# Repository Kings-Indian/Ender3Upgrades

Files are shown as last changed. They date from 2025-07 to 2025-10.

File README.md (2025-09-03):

# Raspberry Pi Magnetic PETG Case for Ender 3

A custom magnetic PETG case designed specifically for the Raspberry Pi Zero 2 W, featuring dual fan cooling, LED support, OPTIONAL screen mount (since people, including me, have computers for their 3D Printers), and camera integration. This case is designed to mount securely to an Ender 3 3D printer for enhanced cooling, monitoring, and lighting capabilities.

## Why I Made This Project

I needed a reliable cooling solution for my Raspberry Pi Zero 2 W that was running Klipper firmware for my Ender 3 printer. The standard cases available didn't provide adequate cooling for the continuous operation required during long print jobs. I also wanted to add LED lighting, a screen mount for better monitoring, and camera integration for timelapses. The magnetic attachment system makes it easy to remove and maintain without tools, while the modular design allows for easy upgrades and modifications.

## Features

- **Magnetic Attachment**: Tool-less assembly using neodymium magnets for easy maintenance
- **Dual 30mm Fans**: Perfect cooling for the Raspberry Pi Zero 2 W during long print jobs
- **LED Integration**: WS2812B strip support for ambient lighting and SK6812 RGBW strips for printer illumination
- **Modular Screen Mount**: Compatible with Waveshare 4.3" HDMI LCD for monitoring
- **Camera Mount**: Adjustable Raspberry Pi Camera Module 3 mount for 4K timelapses
- **Sound Dampening**: Integrated foam ball holders for vibration reduction
- **Cable Management**: Dedicated cable routing holes and access points
- **Klipper Integration**: Smart magnet cover printing using Klipper firmware

## Project Pictures
My current full assembly, in CAD:



### Screen Mount
Screen Mount Assembly (only really useful if u don thave a computer connected)

If you have a computer connected to your printer, this is HIGHLY RECOMMENDED: 



### Camera Integration
Camera Mount Assembly

### LED Lighting System


## Wiring Diagram

```
Raspberry Pi Zero 2 W
├── GPIO 18 → WS2812B LED Strip Data (printer lighting)
├── GPIO 21 → SK6812 RGBW <img width="1018" height="674" alt="463837668-74d05153-4630-4f8c-87a0-d8d51d3b4930" src="https://github.com/user-attachments/assets/d8a1b71c-9329-4780-9d65-e9ff1aa41fdf" />
Strip Data 
├── 5V → WS2812B LED Strip VCC
├── External 5V → SK6812 RGBW Strip VCC
├── GND → WS2812B LED Strip GND
├── External GND → SK6812 LED Strip GND
├── GND → SK6812 RGBW Strip GND
├── Micro HDMI → Waveshare 4.3" LCD
├── Camera Port → Raspberry Pi Camera Module 3
├── 5v →  Fan VCC
├──  GND → Fan GND
└── Micro USB → Power Supply
```
Wiring Diagram

)463837668-74d05153-4630-4f8c-87a0-d8d51d3b4930

## Bill of Materials (BOM
| Item No. | Product Name | Amazon Link | Quantity | Cost (USD) | Notes | Running Total (USD) |
|---|---|---|---|---|---|---|
| 1 | Transparent Polymaker PETG Filament | [Link](https://www.amazon.com/dp/B09DKMCNMW?tag=all3dptrx00131-20&th=1) | 1 | $22.99 | Clear PETG filament for 3D printing | $22.99 |
| 2 | WINSINN 30mm RGB Fan 5V (Pack of 4Pcs) | [Link](https://www.amazon.com/WINSINN-Hydraulic-Bearing-Brushless-30x10mm/dp/B087QDRKW9/) | 1 | $8.99 | RGB micro fans for electronics/3D printing | $31.98 |
| 3 | Waveshare 4.3inch Capacitive Touch Screen LCD | [Link](https://www.amazon.com/4-3inch-HDMI-LCD-Resolution-Capacitive/dp/B07MB9MYYS/) | 1 | $53.99 | Touch display compatible with Raspberry Pi | $85.97 |
| 4 | Neodymium Magnets 5mm x 3mm (60 Pack) | [Link](https://www.amazon.com/Magnets-Multi-use-Refrigerator-Neodymium-Whiteboard/dp/B0BJDZRHV7/) | 1 | $3.99 | Mini magnets for mounting and DIY | $89.96 |
| 5 | Raspberry Pi 02w | [Link](https://www.amazon.com/dp/B0DRRRZBMP?ref_=ppx_hzsearch_conn_dt_b_fed_asin_title_1) | 1 | $26.99 | Main single-board controller | $116.95 |
| 6 | SEZO WS2812B LED Strip Light 1M | [Link](https://www.amazon.com/SEZO-Individually-Addressable-Programmable-Non-Waterproof/dp/B097BX7LRT/) | 1 | $6.99 | Addressable RGB LED strip for effects | $123.94 |
| 7 | Ktehloy 400Pcs Threaded Inserts | [Link](https://www.amazon.com/mxuteuk-420PCS-Screws-Socket-Wrench/dp/B0CSWD34KJ/) | 1 | $13.49 | Brass heat-set inserts for plastic parts | $137.43 |
| 8 | mxuteuk M3 Screws Kit (420PCS) | [Link](https://www.amazon.com/TOP-VIGOR-Machine-Fastener-Motorcycle-Repairment/dp/B0D5CJXW8X/) | 1 | $9.99 | Assorted M3 screws for Pi and mounts | $147.42 |
| 9 | TOP-VIGOR M4-0.7 x 12mm Socket Screws (30PCS) | [Link](https://www.amazon.com/TOP-VIGOR-Machine-Fastener-Motorcycle-Repairment/dp/B0D5CJXW8X/) | 1 | $5.35 | Screws for camera mounting | $152.77 |
| 10 | Arducam Raspberry Pi Camera Module 3 | [Link](https://www.amazon.com/Arducam-Raspberry-Camera-Autofocus-15-22pin/dp/B0C9PYCV9S/) | 1 | $22.00 | 12MP autofocus camera for Pi | $174.77 |
| 11 | UeeKKoo DSI FPC Flexible Cable | [Link](https://www.amazon.com/UeeKKoo-Flexible-Raspberry-Display-Suitable/dp/B0D12TMQ6D/) | 1 | $4.99 | Ribbon cable for Raspberry Pi display | $179.76 |
| 12 | BTF-LIGHTING SK6812 RGBW LED Strip 1M | [Link](https://www.amazon.com/BTF-LIGHTING-Individually-Addressable-Flexible-Non-waterproof/dp/B079ZT9Q9X/) | 1 | $25.99 | RGBW LED strip with addressable control | $205.75 |
| 13 | Zugar Land Galaxy Foam Stress Balls (4 Pack) | [Link](https://www.amazon.com/Zugar-Land-Squeeze-Relaxable-Calming/dp/B0CZS91TNW/) | 1 | $6.99 | Stress relief or soft bumper component | $212.74 |

Total project development time: **23.5 hours**



**Youtube:**: [Link](https://youtube.com/shorts/PC3ZzvA6rok) 

**Reddit:**: [Link](https://www.reddit.com/r/Hack_Club/comments/1m0td3w/my_first_robot_beginner_tank_drive_based_robot/)

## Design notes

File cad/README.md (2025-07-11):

# CAD Source Files

This directory contains the CAD source files for the Raspberry Pi Magnetic PETG Case project.

## File Structure

### Main Directory
- `EnderUpgrades.zip` - Compressed archive containing all CAD files
- `README.md` - This documentation file

### EnderUpgrades Directory
The main project directory containing all component files organized by category:

#### PiControl+Case/
Core case components for the Raspberry Pi enclosure:
- `Case - PiCase.step` - Main Raspberry Pi 
- `Case - FanCase.step` - Fan housing
- `Case - ScreenMount.step` - Screen mounting 

#### LED/
Lighting system components:
- `LED Rail - Open.step` - LED strip mounting rail (left closed side)
- `LED Rail - Closed.step` - LED strip mounting rail (right open side)

#### Camera/
Camera mounting and positioning components:
- `CAM - Fixed.step` - Pi Case Mount 
- `CAM - Rotating Cam Holder.step` - Adjustable rotating camera holder
- `CAMCap.step` - Camera lens cover/protection component

#### Foam Ball Holder/
Vibration damping and support components:
- `foam ball holder - BallHolder.step` - Foam ball holder for vibration isolation

#### Assembly Files
- `Full Assembly.step` - Complete assembly showing all components together

## CAD Software

These files were created using Onshape at https://cad.onshape.com/documents/c014fa01068b7641a56239ac/w/543cb7cab706bdd0461ab360/e/c9c7937bcc8a5b3a582f31b2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 and exported in STEP format.

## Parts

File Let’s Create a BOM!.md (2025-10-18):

### As you create hardware projects for Blueprint, you will be required to include a BOM, or Bill of Materials, in .csv format. If you have any questions or suggestions, reach out in #blueprint-support or DM @Tanishq Goyal!

--- 
## What is a BOM? Why is this important?

A BOM, or Bill of Materials, is the comprehensive list of ==**all**== required parts that you need to manufacture a finished product. Writing a BOM involves creating a document with a clear, organized structure to list all components, parts, and raw materials needed to manufacture a product. Think of this as a recipe: you need to specify exactly how much of each ingredient is needed, along with accurate costs, to ensure the final product turns out correctly. This is one of the most important parts of an open-source hardware project, as it is impossible to build anything without materials. 

--- 
## What Is Included in Your BOM? 

In industrial BOMs, you will generally include information such as part numbers, part names, descriptions, manufacturer/manufacturing method, etc. If you are interested, check out [this BOM writing guide](https://durolabs.co/blog/bill-of-materials-example/)

![[Pasted image 20251017223635.png]]
>[!info] This is is what industry BOMs look like. Thankfully, you won't have to deal with that for Blueprint! This format is pretty widespread, with robotics teams listing parts similarly as well. 

However, for Blueprint, your BOMs will look vastly different and is much less complex.  Here are the bare minimums for what you need for your Blueprint BOM:

1. Product name
2. Product link
3. Product cost
4. Product amount

That's it! However, a good BOM exceeds the bare minimum requirement. A good BOM may include:

1. Product name
2. Product description
3. Product link
4. Product unit price
5. Product amount
6. Product running total.

I find that this format allows me to track my costs easily. Although the minimum BOM looks simpler, the second example is much easier to actually use and read as you work on your project. 

Here's an example! Note that these are flexible. I also included taxes in order to get the most accurate BOM possible. 

| Item | Description | Quantity | Unit Price ($) | Total Price ($) | URL | Running Total ($ with Tax) | |
| --- | --- | --- | --- | --- | --- | --- | --- |
| Lancer Long Hotend | Hotend | 1 | 34.99 | 34.99 | https://peopoly.net/products/magneto-x-lancer-melt-zone?variant=46839304225050 | 37.31 | |
| CPAP FAN | Part-cooling Fan | 1 | 19.99 | 19.99 | https://www.fabreeko.com/products/cpap-fan-10ws7040-hose-by-mellow | 58.62 | |
| 3010 FAN | Hotend Fan | 1 | 6.69 | 6.69 | https://www.aliexpress.us/item/3256808756746945.html | 65.78 | |
| BTT Microprobe | Bed-Leveling Probe | 1 | 18.99 | 18.99 | https://biqu.equipment/products/microprobe-v1-0-for-b1-printers-h2-extruders-ender-3 | 86.00 | |
| SKR Mini E3 V3.0 | MCU | 1 | 29.98 | 29.98 | https://biqu.equipment/products/bigtreetech-skr-mini-e3-v2-0-32-bit-control-board-for-ender-3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 | 117.97 | |
| MGN12H Linear Rail Carriage Block | Linear Rail | 1 | 22.93 | 22.93 | https://www.aliexpress.us/item/2251832643511407.html | 142.42 | |
| GT2 Timing Belt | Belt | 1 | 2.38 | 2.38 | https://www.aliexpress.us/item/3256805030553800.html | 144.96 | |

--- 

## How Do I Create a BOM?

Fortunately, there are tools that allow you to easily create a .csv file, without manually writing one. 

Here is an example using Google Sheets. I will use formulas to make the Total Price and Running Total automatically update. 

1. Total Price Formula. This is equivalent to the Unit Price times the quantity. 
![[Pasted image 20251017234942.png]]
You should then drag the blue circle on the bottom right corner to copy the formulas for the below cells. For more information on formatting with Google Sheets, check out this [basic Google Sheets formula guide!](https://www.youtube.com/watch?v=llkP9DxRAPI) 

2. Running Total. 
This calculation represents the cumulative total of purchases including sales tax. The formula is:

**Running Total = (Total Price × (1 + Sales Tax Rate)) + Previous Running Total**

##### Example: New Jersey Sales Tax (6.625%)

**Formula Structure:**
- **Tax Multiplier:** `1.06625` (1 + 0.06625)
- **Rounding:** Applied to nearest cent using `ROUND` function
- **First Item:** `=ROUND(Total Price × 1.06625, 2)`
  - **Example:** `=ROUND(D2*1.06625,2)`
  - ![[Pasted image 20251018003730.png]]
- **Subsequent Items:** `=ROUND(Total Price × 1.06625, 2) + Previous Running Total`
  - **Example:** `=ROUND(D3*1.06625,2)+G2`
  - ![[Pasted image 20251018003712.png]]

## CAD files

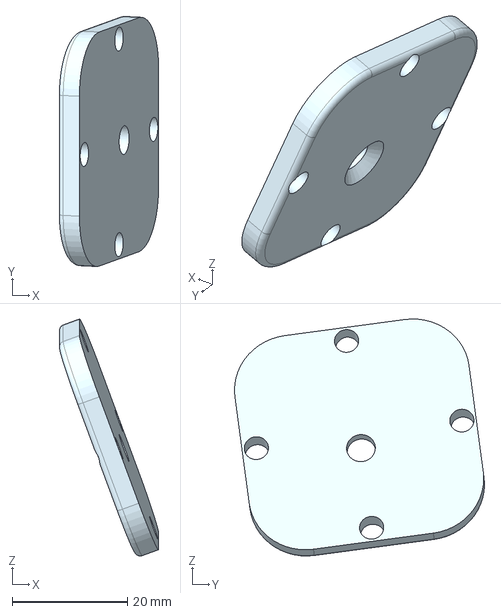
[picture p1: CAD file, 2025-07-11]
cad/EnderUpgrades/Camera/CAMCap.step
17.2 x 43.4 x 41.1 mm

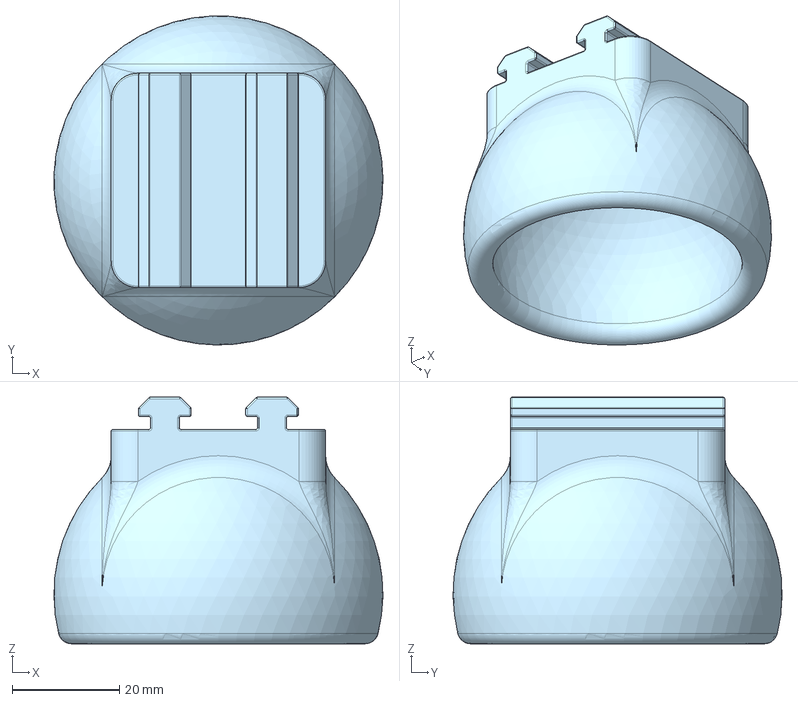
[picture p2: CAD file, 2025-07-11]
cad/EnderUpgrades/Foam Ball Holder/foam ball holder - BallHolder.step
61.4 x 61.4 x 46.0 mm

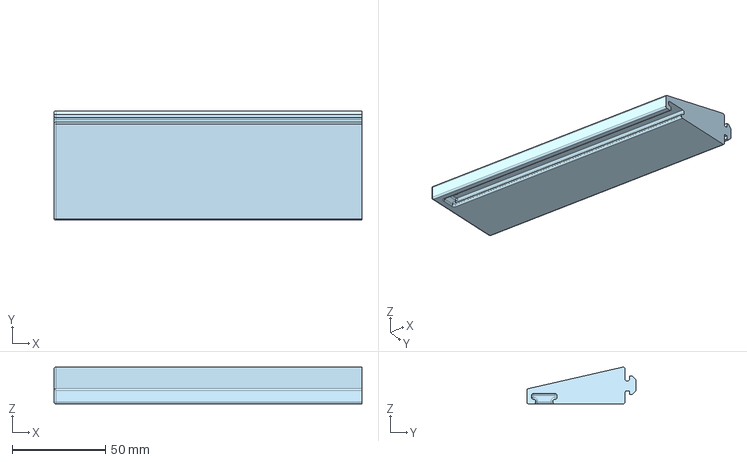
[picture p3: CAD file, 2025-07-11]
cad/EnderUpgrades/LED/LED Rail - Closed.step
165.0 x 58.7 x 19.7 mm

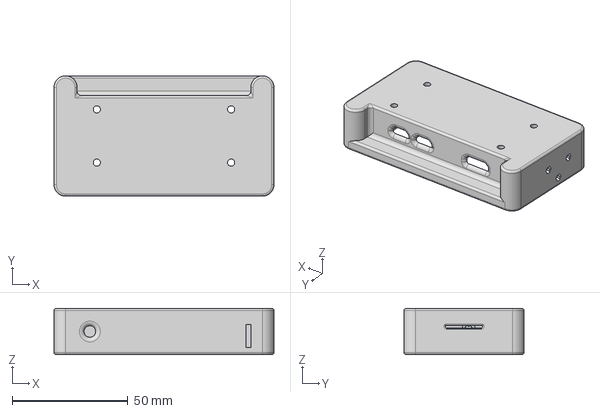
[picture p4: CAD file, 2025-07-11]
cad/EnderUpgrades/PiControl+Case/Case - PiCase.step
95.0 x 52.0 x 20.0 mm

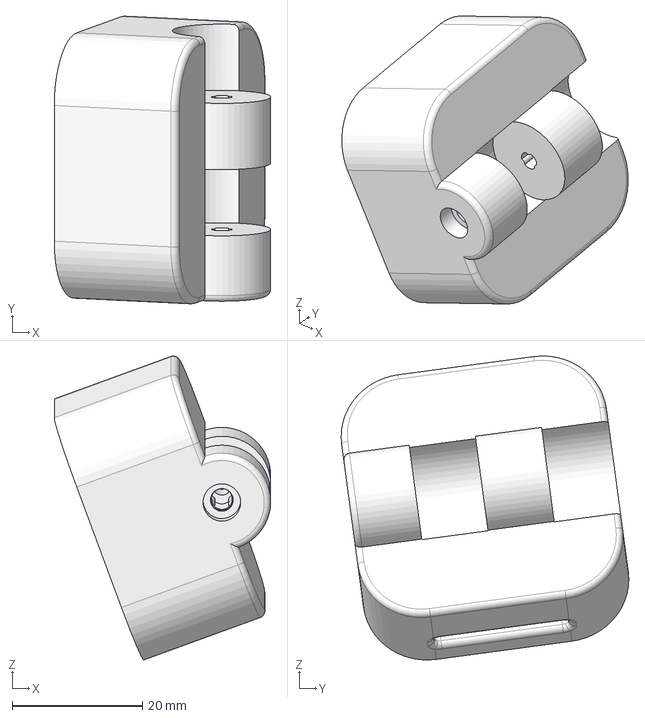
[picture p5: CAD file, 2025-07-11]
cad/EnderUpgrades/Camera/CAM - Rotating Cam Holder.step
33.2 x 44.1 x 46.6 mm

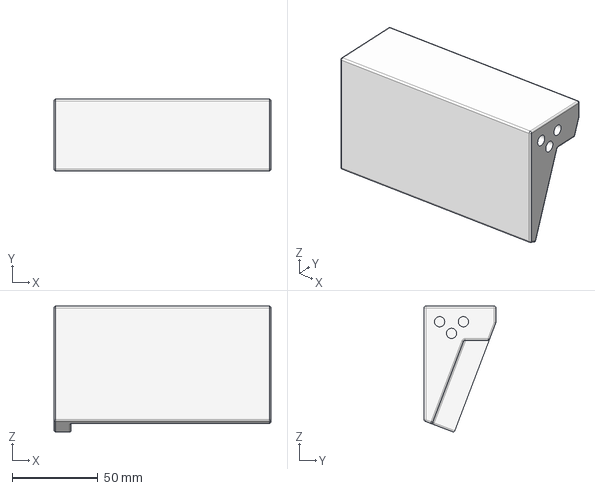
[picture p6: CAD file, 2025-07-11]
cad/EnderUpgrades/PiControl+Case/Case - ScreenMount.step
126.8 x 42.0 x 73.5 mm

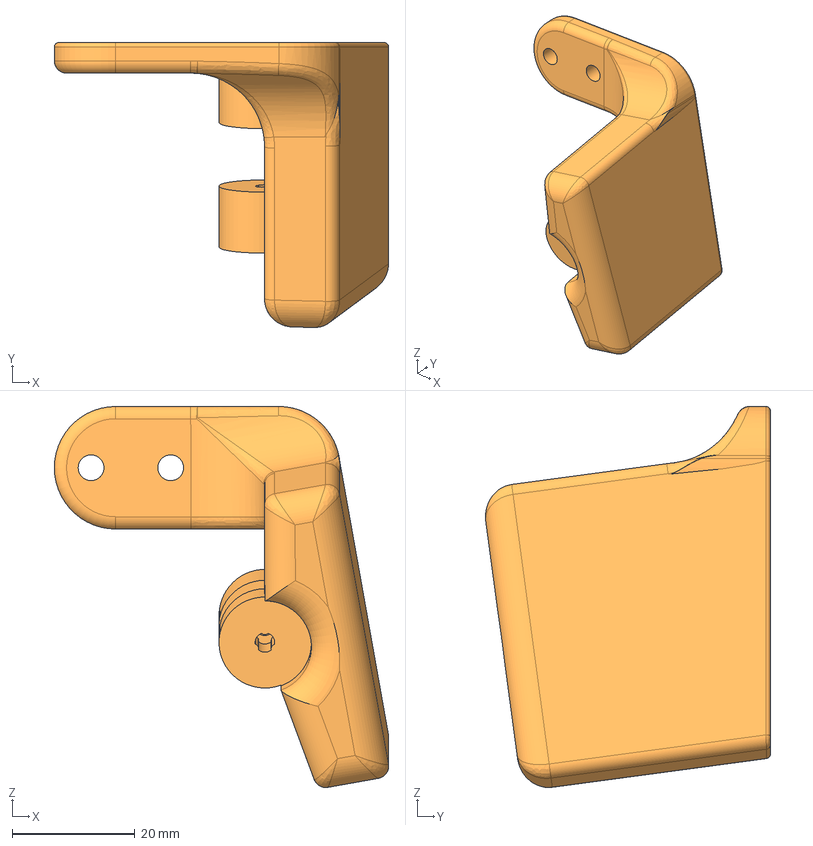
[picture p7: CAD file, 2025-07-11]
cad/EnderUpgrades/Camera/CAM - Fixed.step
54.6 x 46.5 x 62.2 mm

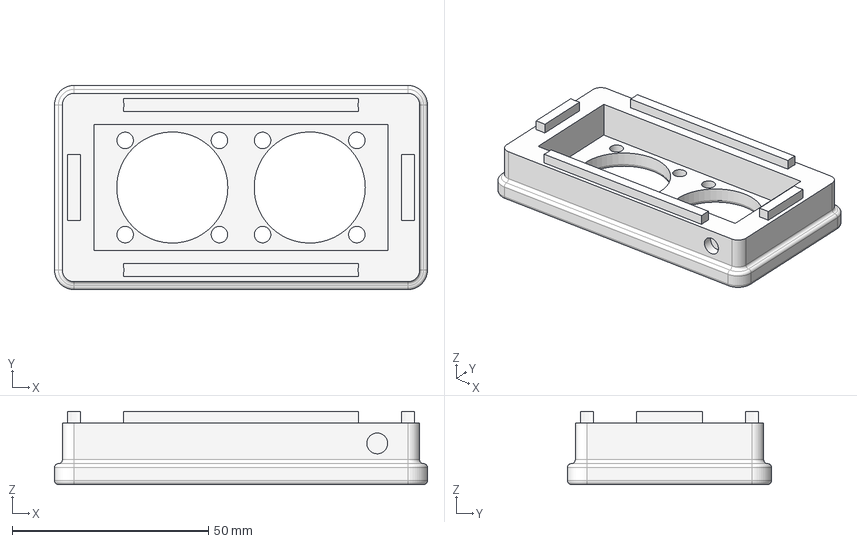
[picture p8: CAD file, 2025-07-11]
cad/EnderUpgrades/PiControl+Case/Case - FanCase.step
95.0 x 52.0 x 18.6 mm

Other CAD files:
cad/EnderUpgrades/LED/LED Rail - Open.step

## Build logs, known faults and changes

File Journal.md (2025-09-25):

---
title: "Raspberry Pi Magnetic PETG Case — Ender 3 Cooling Mod"
author: "Tanishq Goyal"
description: "Custom magnetic PETG case with dual fan cooling, LED support, and modular screen mount for my Ender 3"
created_at: "2025-06-25"
---

# Raspberry Pi Magnetic PETG Case

**Total time spent: 24.5h**

## Goal
Design and print a custom **PETG case for my Ender 3** focused on cooling and modularity.  
Key features:
- Magnetic attachment for easy assembly
- Dual 30mm fans (perfect match for the 30mm × 65mm Raspberry Pi Zero 2 W)
- LED support with WS2812B strips
- Modular screen mount

---

# June 25th: Initial Layout and Planning

Started the design process by planning the overall layout for the Raspberry Pi case. The goal was to create a magnetic PETG case that would fit perfectly on my Ender 3 with dual fan cooling.

This setup allows this layout:

Layout

Designed the fan case conforming with this layout:  
Fan Case 

Added holes to embed **neodymium magnets** for tool-less assembly:  
Magneto
Neodymium Magnets

**Total time spent: 2h**

---

# June 25th: Design Improvements

- Applied fillets for smoother corners  
  Fillets
  Fillet  

Added alignment tabs to ensure proper assembly and prevent misalignment:  
Alignment Tab  
Tab Slot

**Total time spent: 1h**

---

# June 26th: Raspberry Pi Space and Top Cover

#### space for pi 
Side Panel

Designed the top cover to complete the enclosure:  
Top Cover

Added specific Pi mount holes for secure mounting:  
RPi Holes

**Total time spent: 1h**

---

# June 26th: Cable Management

Removed material for easier cable access to make installation and maintenance simpler:  
Cable Opening  
Shaving Detail

Added proper cable holes for clean cable routing:  
Cable Holes

Here's how it looks assembled:  
Assembled View

**Total time spent: 3h**

---

# June 26th: LED Integration

Planned to add rails for WS2812B LED strips to add some nice ambient lighting to the setup:  
LED Rails  
More Rails

**Total time spent: 3h**

---

# June 27th: Screen Mount and LED Rail Redesign

Had some issues with the LED slide design initially. After brainstorming, I realized **neodymium magnets** could provide a sleek, clean, and removable attachment system for the LED strips.

LED Rail Design

**Total time spent: 1h**

---

# June 27th: Screen Mount Design

For the screen, I couldn't find the exact model online. I based my design on this similar model. While I am using 
[Waveshare 4.3" HDMI LCD-B](https://www.waveshare.com/4.3inch-HDMI-LCD-B.htm), the model is of https://www.waveshare.com/4.3inch-dsi-lcd.htm


Added a **10mm margin** on all sides, with a cutout on the right and top for cable clearance:  
  


To enclose the top, I refined the model to match the screen's plane:  


After applying **fillets to all edges**, final design complete:  
  


**Total time spent: 2h**

---

# June 28th: Klipper Integration for Magnet Covers

I realised instead of gluing it in, I can print over it by simply adding a "stop" command in klipper!

Firs,t I added a variable of the amt of layers of PLA. For now, for 2 layers, im using 0.4 mm. With too much layers, im scared of loss of magnetic connection. Then, Ill just cover it as such:




[insert pictures of what you're working on!]

**Total time spent: 0.5h**

---

# June 29th: Design Refinements

I realised how bad this cover is. I believe it deserves more love
 (this one is fine )

Since there just for allignment, ill make them much smaller and farther form the magnets.
I redid that part with a simular idea:


I also realized how hard it is to read, so I reorganized the features




I then fixed up the assembly once more:





**Total time spent: 1.5h**

---

# June 29th: Camera Mount Planning

I also decided to add camera mounts and leds to the printer for lighting.
After a lot of thought, I will start modeling the Rasberry Pi 3 camera mount. Although the right side is easier to model with, soley due to my current setup I am modeling everything on the left. 
First, I incrased the space it has for flexability and for the SD Card and camera. 

After looking at joints, it seems a typical butt hinge and other common hinges arent good for my purpose (based off https://www.youtube.com/watch?v=fbY7xHGaeNM.) I will try to make a design similar to a normal door hinge to increase traction, allowing the pi to be held in place:



First, I decided to keep it only rotatable on the z axis. There was no real reason I saw I would want motion on the Y axis, since I want the nozzle always centered. I also wanted to keep the camera from hitting the toolhead, the FOV from seeing the Z Pole , and planned to mount it to the tensioner. This transalates to my sketch:

|
I am accounting for the space betweeb the lense and back of the pi as tolerance for the pi not hitting the z Gantry. 

I chose the Raspberry Pi Camera Module 3 over the other Pi models because it delivers sharper 4K timelapses, handles low-light printing conditions better with its f/1.8 aperture, and offers autofocus flexibility. Due to the 120 Percent fov, I ex pect to angle it at about 60 sdegrees. For adjustments I still want the ability to rotat ed on the Z Axis. 

FOV at 60 degrees

Regardless, I will design this at 90 degrees for now since rotation is always possible. 

**Total time spent: 2h**

---

# July 6th: Camera Mount Design

I decided to model it at the 20 degrees (I saw the FOV wrong) with 20 degrees of mobility in both directions. Long term, I will likely use a non adjustAbble mount 

Updated sketches:





This mount lets me hasve a strong connection while letting me rotated the needed amount|

This is the fional roptating camera mount


Hole for RPI Camera:



I will fasten it with a 40 mm m3 screw



**Total time spent: 2h**

---

# July 7th: Camera Mount Finalization

This is the finalized rotating camera mount




I decided to change tghe adjustabilty so the bottom angle is 20 degrees isnteadof 40:






There isnt a danger opf the mount hitting the borttom extrusion, as there is only 16 mm of difference in the z axis:



with the klipepr case:


now I just need to add LEDS for the Ender 3 top 2020 profile bar:



Since it should be bright, lighting up the build plate, I will use SK6812 leds due to its dedicated white channel for better white light (more clear video)

although I can thread it through the 2020 profile (its 10 mm, thus fitting within the 10.420mm indent of the profiles) I thought a dedicated LED sleeve would make more sense, as it would be more directly over the toolhead. This is roughly 50 mm of distance from the extrusion.

The profile is very confusing. After a lot of researched I stumbled upon cad which I would use for the lights to see how much the hole which lets the lwds be seeb has to be. However, it doesnt seem to be for tthese given the visual scale (led dimensions are Product Dimensions:1000x2.13x12.0mm in https://www.amazon.com/BTF-LIGHTING-Individually-Addressable-Flexible-Non-waterproof/dp/B01MYV70QZ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):





Instead, ill assume the led is 8mm wide. While its nto best cad practice, I dont think i havea  better option and it shouldnt matter too much:

 (while height dimensions might be wrong, for my purposes, it shouldnt matter. I plan to give it a 3 mm hole regardless. )



I spent a while trying to figure it out but for some reaon the sketch would be solid so i just used the use feature to make ti solid in a different sketch:





for printing, ill split it into 2 even blocks. Ill also enclose one end on the shelf:



After applying fillets, it should be done:






**Total time spent: 3h**

---

# July 7th: Wiring and LED Integration

beyond this, all I have left is wiring. First, I will create a hole in the RPI case for the SK6812 LEDS:





**Total time spent: 1h**

---

# July 8th: Sound Dampening with Foam Balls

I decided to add measures against the high sounds the printer creates, as it makes it harder for me to sleep. First, I decided to add 2 inch foam balls, due to therir springiness and ability to absorb viberations. 

Here is the foam ball holder



**Total time spent: 1h**

# July 8th: Sound Dampening with Foam Balls

I decided to add measures against the high sounds the printer creates, as it makes it harder for me to sleep. First, I decided to add 2 inch foam balls, due to therir springiness and ability to absorb viberations. 

Here is the foam ball holder



**Total time spent: 1h**

# July 10th: Printing everything

I got everything printed
**Total time spent: 1h**

# July 11th: Assembled the pi case

I assembled the Pi case! This includes soldering the wires. I also reideraated on the cad to add more space for the pins and female arduino pins. I also assembled the Pi Mount. 

For the 3d print, I had to melt the magnet into the print a little with a soldering iron.

1. I added the brass threaded inserts
2. I screwed in the pi to the brass threaded inserts
3. I cut female-to-female arduino wires in half
4. I soldered the fan wires to the female ardiono halfs to connect it to the RPI

I also printed the LED bar parts and put them in. I measured and cut the LED Strip, then slid it in as well. 
 **Total time spent: 2h**

# July 26th: Got the Pi and LEDs Working
I got the camera assembled! The assembly was pretty basic, I just put the brass inserts in and snapped them both in place. I screwed in the camera and plugged it in to the RPI. I then attached it to the tensioner part of the ender 3 x axis, and re-tensioned it. 

It turns out, the screw to hold the 2 parts of the camera case isnt needed because the friction of the pressfit is enough to hold it in place. 

I spent some time soldering the LED strip to a whatever this is 





I got the LED macros working! for the camera, i had to get a bit of help, but I got it working as well :) 


I also soldered the LED strip for the Pi Case, which I did twice because the first time was horrid. 





**Total time spent: 3h**

# July 27th: Got the Pi and LEDs Working

Finished the assembly: 

I also printed the feet and slide the foam balls in them :) 

 









**Total time spent: 2h**

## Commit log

2025-06-28 added stuff :D
    [BOM.csv, case_main.step, case_top.step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]
2025-06-30 Remove placeholder STEP files for CAD models: case_main.step, case_top.step, and fan_grill.step.
    [case_main.step, case_top.step, fan_grill.step]
2025-07-11 added cad
2025-09-12 Document assembly process and time spent on tasks
    Added details about assembly steps and time spent on various tasks related to the Raspberry Pi project.
2025-09-17 Enhance journal entries with assembly details
    Added details about measuring and cutting the LED strip, and attaching the camera to the tensioner of the Ender 3 X axis.
2025-09-17 Update Journal with camera assembly details
    Clarified the need for the screw in the camera case and noted the soldering process for the LED strip.
